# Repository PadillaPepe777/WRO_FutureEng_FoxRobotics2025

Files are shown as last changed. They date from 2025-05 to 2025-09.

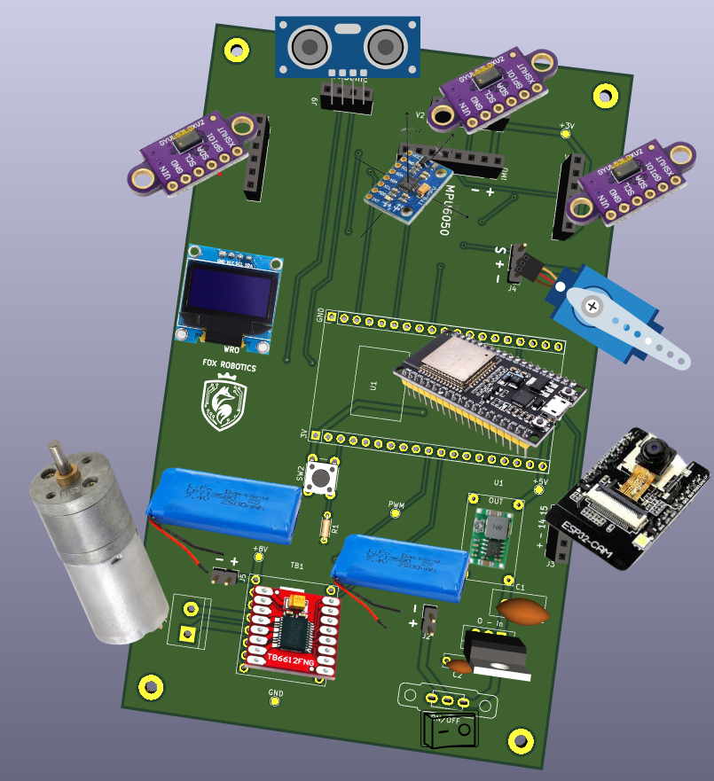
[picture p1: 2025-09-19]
Schemes/CircuitPlusComponents.png

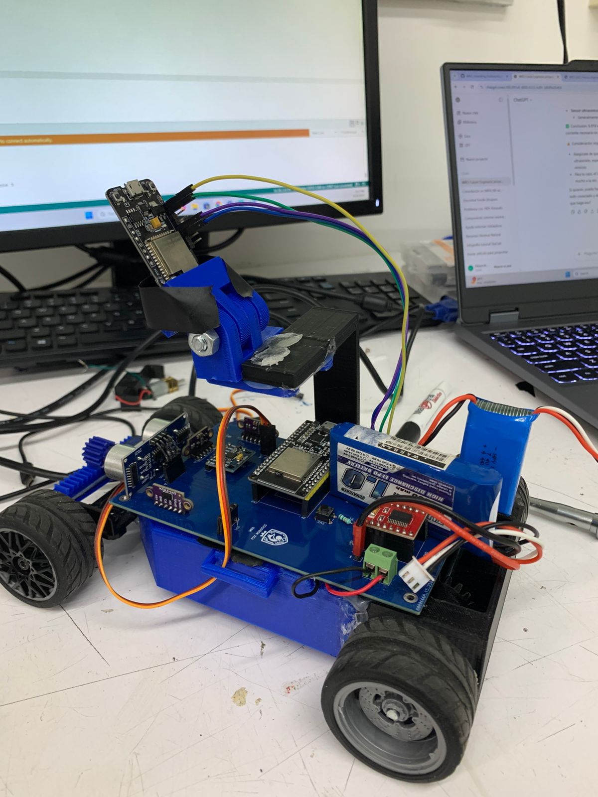
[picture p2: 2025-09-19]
v-photos/Img1.jpg

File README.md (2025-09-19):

The following repository is made with the intention of showing the work made by Luis Rodriguez and Alejandro Padilla for the FUTURE ENGINEERS WRO competition 2025.
The team decided to exploit all the capabilities of the ESP32 microcontroller family capabilities within the possibilities given by the ARDUINO IDE. The main functions of the Autonomous Car are made by the ESP32 WROOM Dev Module, which reads sensors and controls both steering and speed, while the ESP32-CAM its only in charge of color recognition, communicating the data with the ESP32 via Serial Communication. The Way the camera tracks colors is by making the image into kind of a matrix, identifying HSV values, dividing the image in 5-7 sections and communicating what color is the most present and where it’s located.

As it is our first prototype, we did the whole project on a perf board, but there are plans to make it into a professional PCB soon when we gather more resources. The wiring was designed on Ki-CAD, while the mechanical part was made in SolidWorks, a CAD software that our university gives us being students.
The car moves thanks to a Pololu motor in the back part, which pushes both wheels at the same speed thanks to a small gearbox, and the steering is in charge of your typical Servo motor of 90 grams.
The sensors used for the distance measurement were the VL53L0X ToF Infrarred sensors, which work with I2C communication. They have proven to be reliable once adjusted, and even though black objects can cause some trouble, we have worked as a team to find solutions. Apart from them, we are also using an MPU-6050 for accurate turns.

Since we aren’t using a computer like Raspberry, our prototype can run drawing little current, but still, we are using two different batteries to feed the circuit, one is for all the sensing and the brains, while other is just for the motor to run without problems. Both of them are 7.4 volts 600 mAh Li-po batteries, but for one of them we have a 5V regulator to avoid overheating in the microcontrollers. 
One of the attempts to use the ESP32 CAM was using AI with Edge Impulse, but instead of relying on them, we opted to use basic color tracking, which can be seen in the uploaded code. It’s worth noting that we used a version that already has USB compatibility, but the common one with or without Shield should be able to run it the same way. The only downside of this method is that we can’t see the ESP32 CAM view, we can only read what we receive from the Serial Console.

In another version we might unlock the ADC_2 pins to be able to connect to the internet or ESP-NOW for debugging purposes. But as for now we are sticking with what already worked for use, and this code can be useful for anyone trying to use Servos and Motors at the same time, because it’s quite different from Arduino and a bit harder to get this done in a ESP32.

Worth Mentioning This program works for the ESP32 board version 3.1.3

Latest Version can be found at WRO_Tijuana_Sept Folder

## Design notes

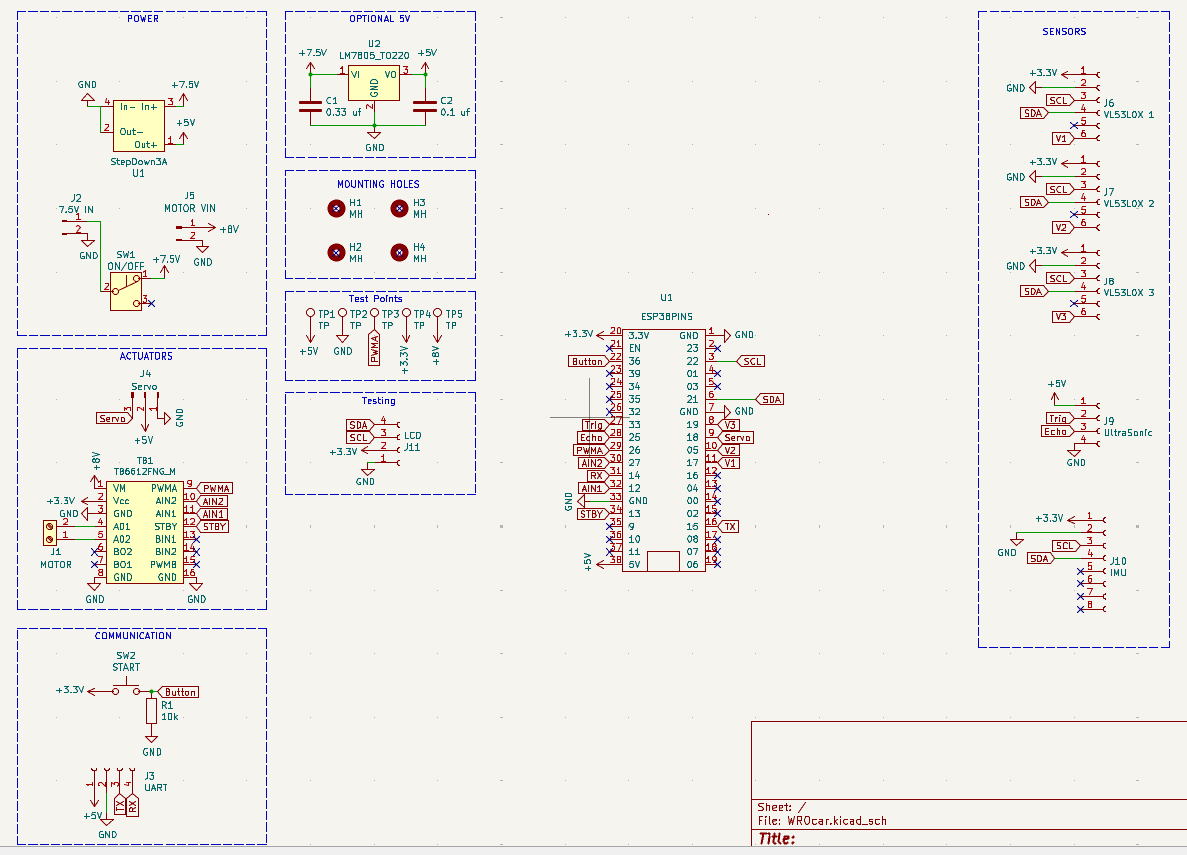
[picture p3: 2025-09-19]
Schemes/Schematic.png

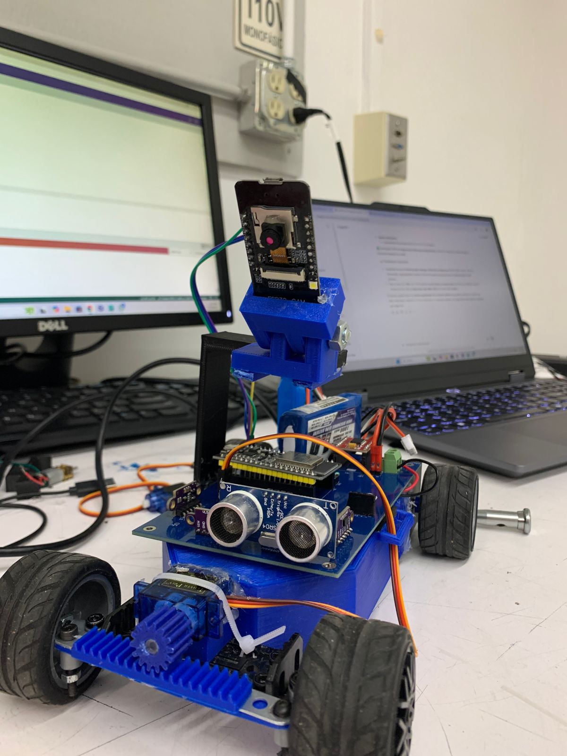
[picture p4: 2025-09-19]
v-photos/Im3.jpg

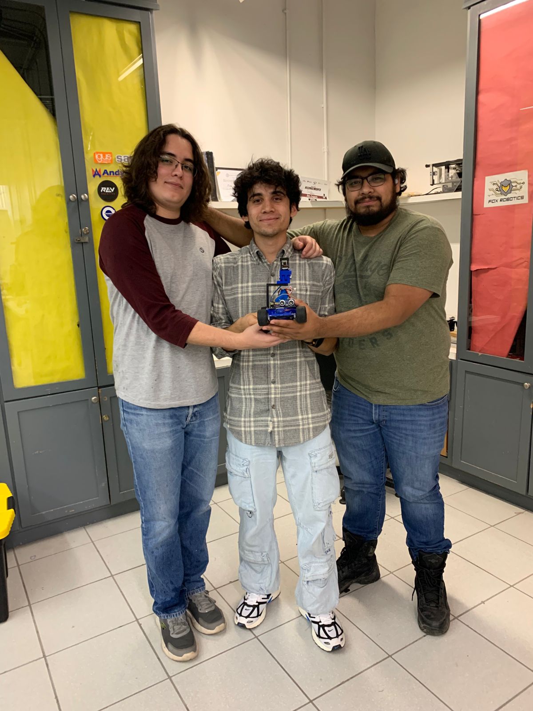
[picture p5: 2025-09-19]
t-photos/TeamPhoto.jpg

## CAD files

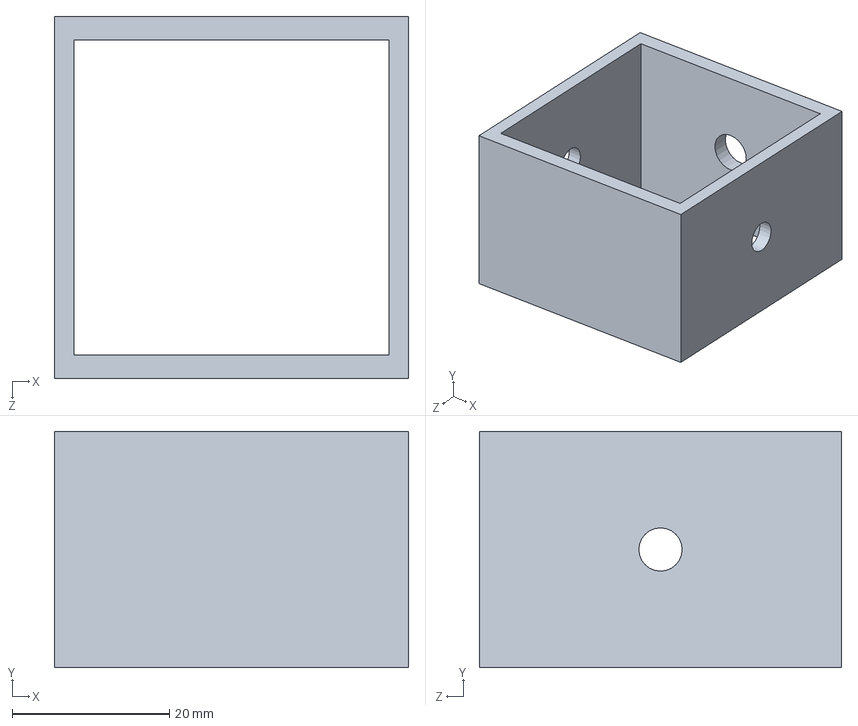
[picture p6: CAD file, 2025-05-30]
Schematic_MechanicalDesign/diferencial1.0.SLDPRT
45.0 x 30.0 x 46.0 mm

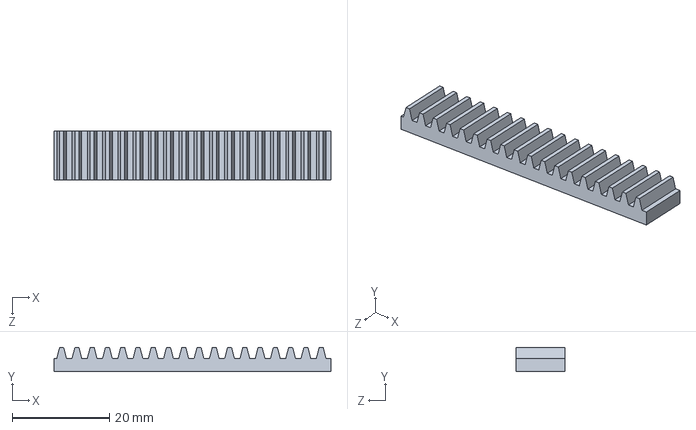
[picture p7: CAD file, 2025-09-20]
WRO_Tijuana_Sept/CAD-CAM/Metric - Rack-spur - rectangular 1M 14.5PA 10FW 4PH 57L---SAll.SLDPRT
57.0 x 5.00 x 10.0 mm

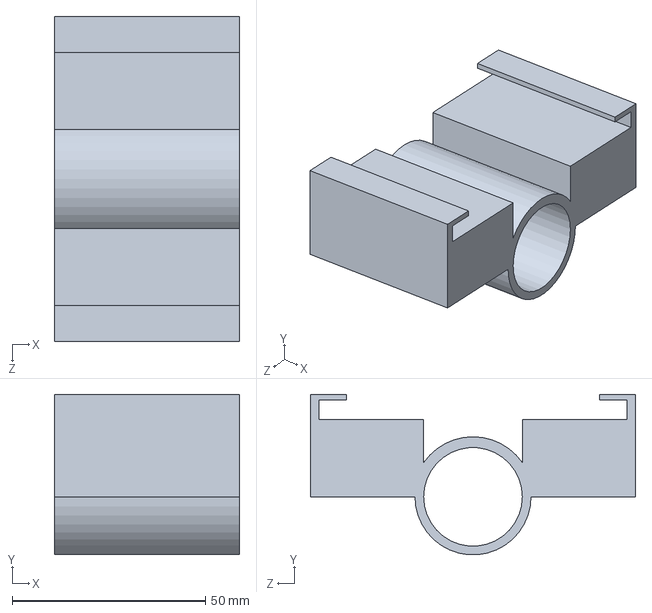
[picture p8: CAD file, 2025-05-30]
Schematic_MechanicalDesign/chasisquenoeschasis.SLDPRT
47.9 x 41.4 x 84.0 mm

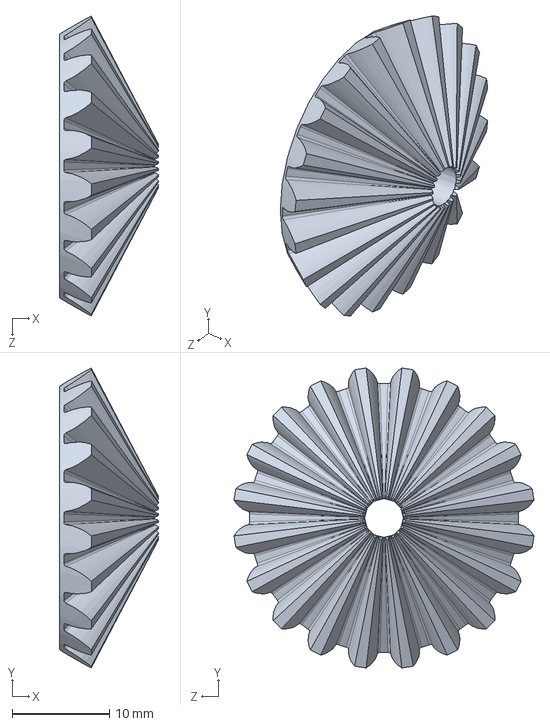
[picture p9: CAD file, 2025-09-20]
WRO_Tijuana_Sept/CAD-CAM/Metric - Straight bevel gear 1.5M 20GT 12PT 20PA 15FW ---20O10H11MD4N.SLDPRT
10.2 x 30.9 x 30.9 mm

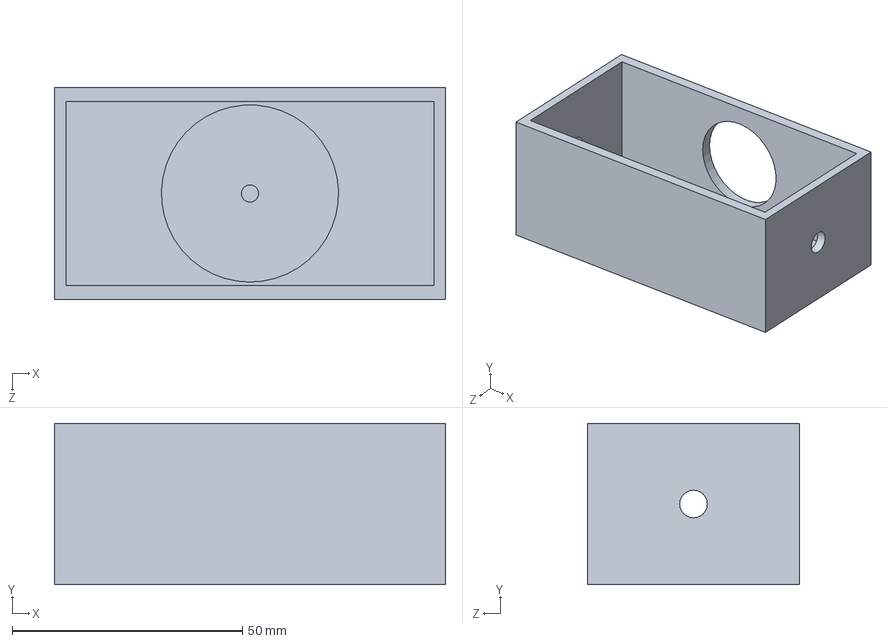
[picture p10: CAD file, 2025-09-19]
WRO_Tijuana_Sept/CAD-CAM/diferencial1.0.SLDPRT
85.0 x 35.0 x 46.0 mm

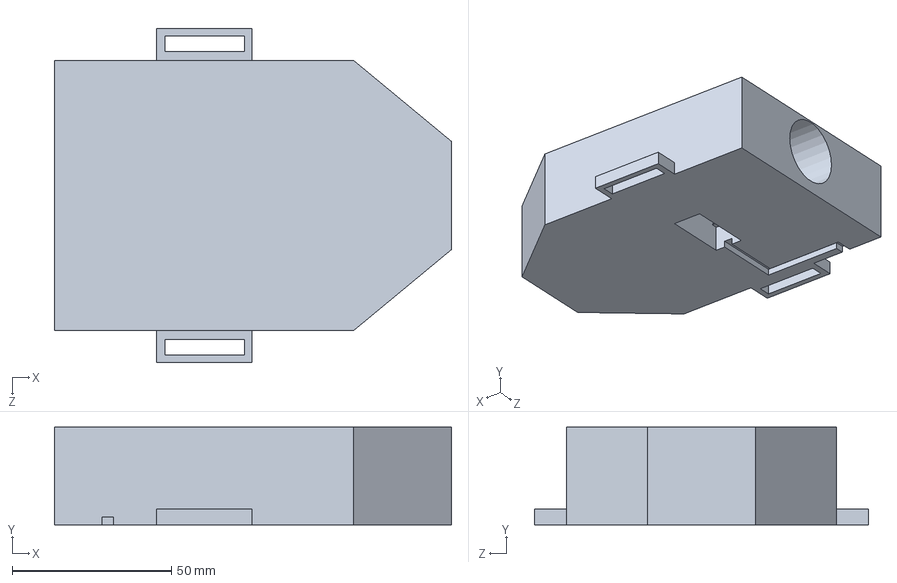
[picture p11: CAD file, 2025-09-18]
WRO_Tijuana_Sept/CAD-CAM/chasis.SLDPRT
124.8 x 30.8 x 105.0 mm

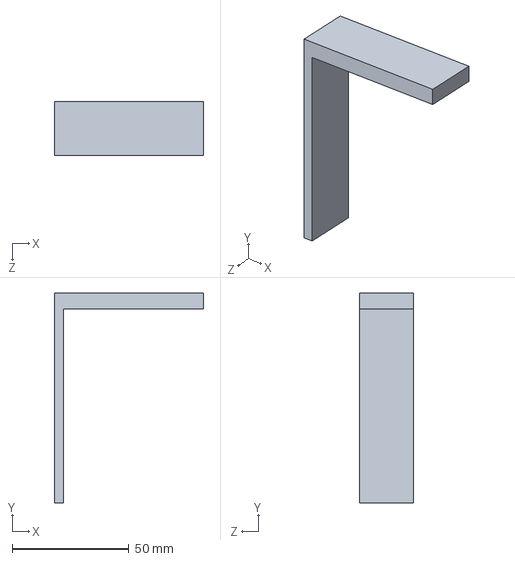
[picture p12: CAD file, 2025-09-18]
WRO_Tijuana_Sept/CAD-CAM/cam_s.SLDPRT
64.0 x 90.0 x 23.0 mm

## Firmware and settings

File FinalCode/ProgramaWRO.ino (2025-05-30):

#include <Arduino.h>

#include <Wire.h>
#include <VL53L0X.h>
#include <ESP32Servo.h>

VL53L0X sensor1; //derecha
VL53L0X sensor2; //delante
VL53L0X sensor3;//izquierda


#define XSHUT1  19  // Pin para apagar sensor 1
#define XSHUT2  5  // Pin para apagar sensor 2
#define XSHUT3  17 // Pin para apagar sensor 3

#define MOTOR_PWM_CHANNEL 2 // canal diferente al del servo
#define MOTOR_PWM_FREQ 12000
#define MOTOR_PWM_RESOLUTION 8

//Comunicacion Serial Colores
#define TX_PIN2 14  // Pin TX personalizado
#define RX_PIN2 15  // No se usa en el transmisor

int Numeros=0, Sector=0, Color=0;

String NOMBRE_COLORES[4] = {"Nada","Rojo", "Verde", "Magenta"};

float DERECHA, ENFRENTE, IZQUIERDA;

int dif,pos;
//Para Control PD
unsigned long currentTime, previousTime;
float elapsedTime;
double error, lastError, cumError, rateError;
//Distancia deseada
float Setpoint=0;
//Variables a Cambiar
float kp=3.8, kd=0.0001 ;

//IMU
int16_t Gyr_rawZ; //Read first Raw Data
float EgZ; //Data different from 0, avoids nan
float GradoRaw;
float AnguloZ=0.0;

unsigned long time1, timePrev, despliegue; //millis for integrals
//despliegue for showing angle every given time
float elapsedTime2;
float rad_to_deg = 180/3.141592654;
unsigned long Tvuelta;

float desired_angle = 0;

//Servo
int servoPin = 18;
Servo servo;

bool listo=false, listo2=false;
int casos=0;
float inicial=0.0;
int Esq=1, Vuelta=0;


//Motor
const int STBY=13;
const int PWM=27;
const int IN1=12;
const int IN2=26;
int Vel=170;

//Auxiliares
int i;
int ColorAnt, SectorAnt;
float auxColor, auxSector;
bool ModoColor=false;
float DLim=50, mult=0.75;

//Para serial
String linea;
String mensaje;


void setup() {


    Serial.begin(115200);
    delay(100);
    Serial2.begin(115200, SERIAL_8N1, RX_PIN2, TX_PIN2);
    Wire.begin(); //  SDA y SCL 40kHz
    delay(100);

    // Configurar pines XSHUT como salida
    pinMode(XSHUT1, OUTPUT);
    pinMode(XSHUT2, OUTPUT);
    pinMode(XSHUT3, OUTPUT);

    // Apagar ambos sensores
    digitalWrite(XSHUT1, LOW);
    digitalWrite(XSHUT2, LOW);
    digitalWrite(XSHUT3, LOW);
    delay(10);

    // Encender y configurar el primer sensor
    digitalWrite(XSHUT1, HIGH);
    delay(10);
    sensor1.setAddress(0x30);  // Cambiar dirección del sensor 1
    if (!sensor1.init()) {
        Serial.println("Error al iniciar Sensor 1");
    } else {
        Serial.println("Sensor 1 iniciado correctamente");
    }

    // Encender y configurar el segundo sensor
    digitalWrite(XSHUT2, HIGH);
    delay(10);
    sensor2.setAddress(0x31);  // Cambiar dirección del sensor 2
    if (!sensor2.init()) {
        Serial.println("Error al iniciar Sensor 2");
    } else {
        Serial.println("Sensor 2 iniciado correctamente");
    }

    digitalWrite(XSHUT3, HIGH);
    delay(10);
    sensor3.setAddress(0x32);  // Cambiar dirección del sensor 2
    if (!sensor3.init()) {
        Serial.println("Error al iniciar Sensor 3");
    } else {
        Serial.println("Sensor 3 iniciado correctamente");
    }

    // Iniciar medición en ambos sensores
    sensor1.startContinuous();
    sensor2.startContinuous();
    sensor3.startContinuous();

delay(100);

EgZ=0.0;

 Wire.beginTransmission(0x68);
    if (Wire.endTransmission() == 0) {  
        Wire.beginTransmission(0x68);
        Wire.write(0x6B);
        Wire.write(0);  // Sacar de modo sleep
        Wire.endTransmission(true);
        Serial.println("MPU6050 iniciado correctamente");
    } else {
        Serial.println("Error: MPU6050 no detectado.");
    }

    for(i=0;i<600;i++)
    {
    anguloIMU();
    EgZ+=Gyr_rawZ;
    delay(1);
    }
    
    EgZ=EgZ/600.0;

    Serial.print("Offsets: ");
    Serial.println(EgZ);

    delay(100);

    timePrev=millis();
    anguloIMUYa();
    Serial.print("Valores al momento: ");
   
        Serial.println(Gyr_rawZ);
        delay(100);

  servo.setPeriodHertz(50);             // 50 Hz para servo
  servo.attach(servoPin, 500, 2400);    // valores típicos: 500us (0°), 2400us (180°)
  Serial.println("Servo listo");

    pinMode(IN1,OUTPUT);
    pinMode(IN2,OUTPUT);
    pinMode(STBY,OUTPUT);
    digitalWrite(IN1, HIGH);
    digitalWrite(IN2, LOW);
    digitalWrite(STBY, HIGH);

ledcAttachChannel(PWM, MOTOR_PWM_FREQ, MOTOR_PWM_RESOLUTION, MOTOR_PWM_CHANNEL);

ledcAttachChannel(18, 50, 10, 1);

  servo.setPeriodHertz(50);
  servo.attach(18, 500, 2400);

 // ledcWrite(PWM, 200);  // valor entre 0-255 para 8 bits

linea ="";
while (linea.length() == 0) {
  if (Serial2.available()) {
    linea = Serial2.readStringUntil('\n');
    linea.trim(); // Limpia espacios y saltos de línea
    Serial.println("Recibido: " + linea);
  }
  delay(50);

}
}


void loop() {

//Habran switch cases para sentido horario, antihorario y colores con ambas variantes
//Para Hacer lo del angulo cuando se cumpla la condicion de pared enfrente, libre al lateral
//Seguir hasta haber una diferencia de 80 grados min entre inicial y actual

//Primero se va a detectar con comunicacion serial si hay colores o no, en caso de que no se ignora y se pasa al siguiente 

if (!listo){

    for(i=0;i<10;i++)
    {
        ReceiveSerial();
        Sector=Numeros%10;
        auxSector+=Sector;
      
          if(Sector==0)
        {
            Serial.println("No hay Color");
        }
          else
        {
            Color=(Numeros/10);
            auxColor+=1; //Para sacar promedio de cuantas veces se detecto color
            //Serial.println("Color: "+NOMBRE_COLORES[Color]+" En Sector "+String(Sector));
        }
    }

    //Aqui Sacamos un promedio de 10 lecturas, solo para comprobar antes de moverse si ve colores, si es asi...
    //podemos activar ModoColo como true, caso contrario leeremos mas adelante para comprobar y desactivar 
    //el modo mas adelante para evitar falsos positivos y consumir recursos

    auxColor=auxColor/10;

    //Mayor a %50 lo damos por bueno
    if(auxColor>0.5){
    ModoColor=true;
    Vel=150;
    }


  setLongRangeMode();
  ENFRENTE=(sensor2.readRangeContinuousMillimeters()/10.0);
  for(i=0; i<=50; i++)
  {
    ENFRENTE=(sensor2.readRangeContinuousMillimeters()/10.0);
    if(ENFRENTE<=300) break;
  }

  if(ENFRENTE>300.0)
  {
    setNormalMode();
    for(i=0; i<=50; i++)
  {
    ENFRENTE=(sensor2.readRangeContinuousMillimeters()/10.0);
    if(ENFRENTE<=300.0) break;
  }
  }

  if(ENFRENTE<=300.0)
  {
    inicial=ENFRENTE;
  }
  else
  {
    inicial=100.0;
  }
  listo=true;
}

setNormalMode();

ledcWrite(PWM, Vel);  // valor entre 0-255 para 8 bits

while(!listo2){

    Distancias();
    ColorAnt=0;

    if(DERECHA>=18 && IZQUIERDA>=18) //Cuidar que no estemos muy pegados 
    {
    ReceiveSerialFull();
    ColorAnt=Color;
    if(Sector>0)
    {
      ReceiveSerialFull();
      if(Sector>0 && ColorAnt==Color)
      {
        ModoColor=true;
        Vel=155;
        ledcWrite(PWM, Vel);  // valor entre 0-255 para 8 bits
        ActoColor();
      }
      else
      {
        Serial.println("Falsa Alarma");
      }
    }
    previousTime=millis();
    }
    else if(ENFRENTE<=DLim && IZQUIERDA>=90)
    {
    pos=10+(ENFRENTE*mult);
    casos=1;
    SetServo();

      delay(1);

      Tvuelta=timePrev=millis();
      while(abs(AnguloZ)<75.0)
      {
        anguloIMUYa();
        Serial.println(AnguloZ);
        if(millis()-Tvuelta>3000)
        break;
      }

      Serial.println("Ya salio");
      AnguloZ=0.0;
      
      pos=90;
      SetServo();
      delay(1);
      Distancias();

      while(IZQUIERDA>=90.0)
      {
        Distancias();
        dif= (DERECHA-35);  //para mantener pegado a un lado en lo que hay otro de referencia
        pos=PD_Centro (dif);
        ReceiveSerialFull();
        if(Sector>0 && (Color>0 && Color<4))
        {
          ReceiveSerialFull();
          if(Sector>0 && (Color>0 && Color<4))
          break;
        }
        Serial.println("Derecho");
      }
        
      previousTime=millis();
      break;
    }
      else if(ENFRENTE<=DLim && DERECHA>=90)
    {
    pos=170-(ENFRENTE*mult);
    casos=2;
    SetServo();
    delay(1);

      Tvuelta=timePrev=millis();
      
      while(abs(AnguloZ)<75.0)
      {
        anguloIMUYa();
        Serial.println(AnguloZ);
        if(millis()-Tvuelta>3000)
        break;
      }
      Serial.println("Ya salio");
      AnguloZ=0.0;

      pos=90;
      SetServo();
      while(DERECHA>=100.0)
      {
        Distancias();
        dif= (35-IZQUIERDA);  //para mantener pegado a un lado en lo que hay otro de referencia
        pos=PD_Centro (dif);

        ReceiveSerialFull(); //Volvemos a checar para evitar falsos positivos
        if(Sector>0 && (Color>0 && Color<4))
        {
          ReceiveSerialFull();
          if(Sector>0 && (Color>0 && Color<4))
          break;
        }
        Serial.println("Derecho");
      }
  
      previousTime=millis();
      break;
    }
    else if(DERECHA<100.0 && IZQUIERDA<100.0)
    {
    dif= (DERECHA-IZQUIERDA);
    pos=PD_Centro (dif);
    if(abs(pos)>4)
    {
    pos=90+pos;
    }
    else
    {
        pos=90;
    }
    }
    else
    pos=90;
    

    SetServo();
    delay(5);
}

listo2=true;

if(casos==1 && ModoColor==true)
casos=3;

if(casos==2 && ModoColor==true)
casos=4;
//Si se acaba la memoria, tal vez hacer los casos e irlos llamando porn turnos en el primer while, luego quedarse en uno solo

    switch(casos) {
      case 1:
      Serial.println("Sentido Antihorario No Color");
      while(Vuelta<3){

          if(Esq==4){
          Vuelta++;
          Esq=0;
          }
          if(Vuelta>=3)
          break;

        Distancias();

        if(ENFRENTE<=DLim && IZQUIERDA>=90)
    {
    pos=10+(ENFRENTE*mult);
    Esq++;
    SetServo();
      delay(1);

      Tvuelta=timePrev=millis();
      
      while(abs(AnguloZ)<75.0)
      {
        anguloIMUYa();
        Serial.println(AnguloZ);
        if(millis()-Tvuelta>3000)
        break;
      }
      Serial.println("Ya salio");
      AnguloZ=0.0;
    
      pos=90;
      SetServo();

      while(IZQUIERDA>=100.0){
        Distancias();
        dif= (DERECHA-35);  //para mantener pegado a un lado en lo que hay otro de referencia
        pos=PD_Centro (dif);
        Serial.println("Derecho");
      }

      previousTime=millis();
      //break;
    }
    else if(DERECHA<100.0 && IZQUIERDA<100.0)
    {
    dif= (DERECHA-IZQUIERDA);
    pos=PD_Centro (dif);

    if(abs(pos)>4)
    pos=90+pos;
    else
    pos=90;
    }
    else
    pos=90;

    SetServo();
    delay(5);

        if(Esq==4){
          Vuelta++;
          Esq=0;
        }
      }

      break;

      case 2:
      Serial.println("Sentido Horario No Color");
            while(Vuelta<3){

          if(Esq==4){
          Vuelta++;
          Esq=0;
          }
          if(Vuelta>=3)
          break;
            
        Distancias();

        if(ENFRENTE<=DLim && DERECHA>=90)
    {
    pos=170-(ENFRENTE*mult);
    Esq++;
    SetServo();
      delay(1);

      Tvuelta=timePrev=millis();
      
      while(abs(AnguloZ)<75.0)
      {
        anguloIMUYa();
        Serial.println(AnguloZ);
        if(millis()-Tvuelta>3000)
        break;
      }
      Serial.println("Ya salio");
      AnguloZ=0.0;
    
      pos=90;
      SetServo();

      while(DERECHA>=100.0){
        Distancias();
        dif= (35-IZQUIERDA);  //para mantener pegado a un lado en lo que hay otro de referencia
        pos=PD_Centro (dif);
        Serial.println("Derecho");
      }

      previousTime=millis();
      //break;
    }
    else if(DERECHA<100.0 && IZQUIERDA<100.0)
    {
    dif= (DERECHA-IZQUIERDA);
    pos=PD_Centro (dif);

    if(abs(pos)>4)
    pos=90+pos;
    else
    pos=90;
    }
    else
    pos=90;

    SetServo();
    delay(5);

        if(Esq==4){
          Vuelta++;
          Esq=0;
        }
      }

      break;

      case 3:

      Serial.println("Sentido Antihorario Color");

      //Estara Complicado
      while(Vuelta<3){

          if(Esq==4){
          Vuelta++;
          Esq=0;
          }
          if(Vuelta>=3)
          break;

          Distancias();
    ColorAnt=0;

    if(DERECHA>=18 && IZQUIERDA>=18) //Cuidar que no estemos muy pegados 
    {
    ReceiveSerialFull();
    ColorAnt=Color;
    if(Sector>0)
    {
      ReceiveSerialFull();
      if(Sector>0 && ColorAnt==Color)
      {
        ModoColor=true;
        Vel=155;
        ledcWrite(PWM, Vel);  // valor entre 0-255 para 8 bits
        ActoColor();
      }
      else
      {
        Serial.println("Falsa Alarma");
      }
    }
    previousTime=millis();
    }
    else if(ENFRENTE<=DLim && IZQUIERDA>=90)
    {
    pos=10+(ENFRENTE*mult);
    Esq++;

    SetServo();

      delay(1);

      Tvuelta=timePrev=millis();
      while(abs(AnguloZ)<75.0)
      {
        anguloIMUYa();
        Serial.println(AnguloZ);
        if(millis()-Tvuelta>3000)
        break;
      }

      Serial.println("Ya salio");
      AnguloZ=0.0;
      
      pos=90;
      SetServo();
      delay(1);
      Distancias();

      while(IZQUIERDA>=90.0)
      {
        Distancias();
        dif= (DERECHA-35);  //para mantener pegado a un lado en lo que hay otro de referencia
        pos=PD_Centro (dif);
        ReceiveSerialFull();
        if(Sector>0 && (Color>0 && Color<4))
        {
          ReceiveSerialFull();
          if(Sector>0 && (Color>0 && Color<4))
          break;
        }
        Serial.println("Derecho");
      }
        
      previousTime=millis();
      //break;
    }
    else if(DERECHA<100.0 && IZQUIERDA<100.0)
    {
    dif= (DERECHA-IZQUIERDA);
    pos=PD_Centro (dif);
    if(abs(pos)>4)
    {
    pos=90+pos;
    }
    else
    {
        pos=90;
    }
    }
    else
    pos=90;
    

    SetServo();
    delay(5);
            if(Esq==4){
          Vuelta++;
          Esq=0;
        }
      }

      break;

      case 4:

      Serial.println("Sentido Horario Color");
      //Definitivamente Complicado

      while(Vuelta<3){

          if(Esq==4){
          Vuelta++;
          Esq=0;
          }
          if(Vuelta>=3)
          break;

      Distancias();
    ColorAnt=0;

    if(DERECHA>=18 && IZQUIERDA>=18) //Cuidar que no estemos muy pegados 
    {
    ReceiveSerialFull();
    ColorAnt=Color;
    if(Sector>0)
    {
      ReceiveSerialFull();
      if(Sector>0 && ColorAnt==Color)
      {
        ModoColor=true;
        Vel=155;
        ledcWrite(PWM, Vel);  // valor entre 0-255 para 8 bits
        ActoColor();
      }
      else
      {
        Serial.println("Falsa Alarma");
      }
    }
    previousTime=millis();
    }
    else if(ENFRENTE<=DLim && IZQUIERDA>=90)
    {
    pos=10+(ENFRENTE*mult);
    casos=1;
    SetServo();

      delay(1);

      Tvuelta=timePrev=millis();
      while(abs(AnguloZ)<75.0)
      {
        anguloIMUYa();
        Serial.println(AnguloZ);
        if(millis()-Tvuelta>3000)
        break;
      }

      Serial.println("Ya salio");
      AnguloZ=0.0;
      
      pos=90;
      SetServo();
      delay(1);
      Distancias();

      while(IZQUIERDA>=90.0)
      {
        Distancias();
        dif= (DERECHA-35);  //para mantener pegado a un lado en lo que hay otro de referencia
        pos=PD_Centro (dif);
        ReceiveSerialFull();
        if(Sector>0 && (Color>0 && Color<4))
        {
          ReceiveSerialFull();
          if(Sector>0 && (Color>0 && Color<4))
          break;
        }
        Serial.println("Derecho");
      }
        
      previousTime=millis();
      break;
    }
      else if(ENFRENTE<=DLim && DERECHA>=90)
    {
    pos=170-(ENFRENTE*mult);
    casos=2;
    SetServo();
    delay(1);

      Tvuelta=timePrev=millis();
      
      while(abs(AnguloZ)<75.0)
      {
        anguloIMUYa();
        Serial.println(AnguloZ);
        if(millis()-Tvuelta>3000)
        break;
      }
      Serial.println("Ya salio");
      AnguloZ=0.0;

      pos=90;
      SetServo();
      while(DERECHA>=100.0)
      {
        Distancias();
        dif= (35-IZQUIERDA);  //para mantener pegado a un lado en lo que hay otro de referencia
        pos=PD_Centro (dif);

        ReceiveSerialFull(); //Volvemos a checar para evitar falsos positivos
        if(Sector>0 && (Color>0 && Color<4))
        {
          ReceiveSerialFull();
          if(Sector>0 && (Color>0 && Color<4))
          break;
        }
        Serial.println("Derecho");
      }
  
      previousTime=millis();
      //break;
    }
    else if(DERECHA<100.0 && IZQUIERDA<100.0)
    {
    dif= (DERECHA-IZQUIERDA);
    pos=PD_Centro (dif);
    if(abs(pos)>4)
    {
    pos=90+pos;
    }
    else
    {
        pos=90;
    }
    }
    else
    pos=90;
    
    SetServo();
    delay(5);

          if(Esq==4){
          Vuelta++;
          Esq=0;
        }

}

      break;

      default:

      Serial.println("Espero esto no suceda");

      break;
    }

    if(casos <=2)
    {
    Distancias();
    servo.write(90);
    Tvuelta=millis();
    while(ENFRENTE<inicial)
    {
      Distancias();
      if(millis()-Tvuelta>=2000)
      break;
    }
    }

    if(casos==3) //Antihorario color
    { 
    Vel=140;
    ledcWrite(PWM, Vel);  // valor entre 0-255 para 8 bits
    Tvuelta=millis();

    while(Color!=4 && Sector<=3)
    {
      Distancias();
      if(DERECHA<=90)
      dif=(DERECHA-IZQUIERDA);
      else
      dif=(35-IZQUIERDA);

      pos=PD_Centro (dif);
      SetServo();

      ReceiveSerialFull();

      if(millis()-Tvuelta>=10000)
      break;;
    }
    pos=150;
    SetServo();
    
    Tvuelta=millis();
    while(ENFRENTE>12.0)
    {
      Distancias();
      if(millis()-Tvuelta>=2000)
      break;
    }
    }

    if(casos==4) //Antihorario color
    { 
    Vel=140;
    ledcWrite(PWM, Vel);  // valor entre 0-255 para 8 bits
    Tvuelta=millis();


    while(Color!=4 && Sector>=3)
    {
      Distancias();
      if(IZQUIERDA<=90)
      dif=(DERECHA-IZQUIERDA);
      else
      dif=(DERECHA-35);
    
      pos=PD_Centro (dif);
      SetServo();

      ReceiveSerialFull();

      if(millis()-Tvuelta>=10000)
      break;
    }
    pos=30;
    SetServo();
    Tvuelta=millis();
    while(ENFRENTE>12.0)
    {
      Distancias();
      if(millis()-Tvuelta>=2000)
      break;
    }
    }

    //FIN DEL PROGRAMA

    Vel=0;
    ledcWrite(PWM, Vel);  // valor entre 0-255 para 8 bits

    while(1)
    {
      Serial.println("Esto es todo amigos");
      delay(500);
    }

    //Si llegan a haber problemas para parkearse, poner otra condicion para buscar magenta en la vuelta 2 Esq 4

}

int PD_Centro (int input) {
 
    currentTime = millis();                          // obtener el tiempo actual
    elapsedTime = (currentTime - previousTime)/1000.0;     // calcular el tiempo transcurrido
        
    error = input;                               // determinar el error entre la consigna y la medición
    rateError = (error - lastError) / elapsedTime;       // calcular la derivada del error
 
    int output = kp*error + kd*rateError;     // calcular la salida del PID

    if(output>50)
    {
      output=50;
    }
    if(output<-50)
    {
      output=-50;
    }

    lastError = error;                                    // almacenar error anterior
    previousTime = currentTime;                           // almacenar el tiempo anterior
 
    return output;
}

void anguloIMUYa () {
   // the previous time is stored before the actual time read
    time1 = millis();  // actual time read
    elapsedTime2 = (time1 - timePrev) / 1000.0; 
    
   Wire.beginTransmission(0x68);
   Wire.write(0x47); //Gyro data first adress
   Wire.endTransmission(false);
   Wire.requestFrom(0x68,2,true); //Just  registers
   
   Gyr_rawZ=Wire.read()<<8|Wire.read();

   GradoRaw=(Gyr_rawZ-EgZ)/131.0;

   if(abs(GradoRaw*elapsedTime2)>=0.06)
   AnguloZ+= GradoRaw*elapsedTime2;

  timePrev = time1;
}


void anguloIMU () {
   // the previous time is stored before the actual time read
    time1 = millis();  // actual time read
    elapsedTime2 = (time1 - timePrev) / 1000.0; 
    
   Wire.beginTransmission(0x68);
   Wire.write(0x47); //Gyro data first adress
   Wire.endTransmission(false);
   Wire.requestFrom(0x68,2,true); //Just  registers
   
   Gyr_rawZ=Wire.read()<<8|Wire.read();

  timePrev = time1;
}

void setLongRangeMode() {
  sensor2.stopContinuous();
  sensor2.setSignalRateLimit(0.1); // menor = más alcance
  sensor2.setVcselPulsePeriod(VL53L0X::VcselPeriodPreRange, 18);
  sensor2.setVcselPulsePeriod(VL53L0X::VcselPeriodFinalRange, 14);
  sensor2.startContinuous();
  Serial.println("Modo: Largo alcance activado");
}

void setNormalMode() {
  sensor2.stopContinuous();
  sensor2.setSignalRateLimit(0.25); // valor por defecto
  sensor2.setVcselPulsePeriod(VL53L0X::VcselPeriodPreRange, 14);
  sensor2.setVcselPulsePeriod(VL53L0X::VcselPeriodFinalRange, 10);
  sensor2.startContinuous();
  Serial.println("Modo: Normal restaurado");
}

void Distancias(){
    DERECHA=(sensor1.readRangeContinuousMillimeters()/10.0)-1.2;
    delay(1);
    ENFRENTE=(sensor2.readRangeContinuousMillimeters()/10.0)-6.5;
    delay(1);
    IZQUIERDA=(sensor3.readRangeContinuousMillimeters()/10.0)-4.3;
    delay(1);

    Serial.print("Distancia Sensor 1: ");
    Serial.print(DERECHA);

    Serial.print("   Distancia Sensor 2: ");
    Serial.print(ENFRENTE);

    Serial.print("   Distancia Sensor 3: ");
    Serial.println(IZQUIERDA);
}

void ReceiveSerial(){

    unsigned long timeout=millis();
    mensaje="";
    while(mensaje.length() == 0) {
    Serial.println("Esperando...");
    if(millis()-timeout>=500)
    break;
    delay(1);
    if (Serial2.available()) {
        mensaje = Serial2.readStringUntil('\n');
        mensaje.trim();
        Numeros = mensaje.toInt();
    }
}
}

void SetServo(){
    if(pos>135)
    pos=135;

    if(pos<45)
    pos=45;

    servo.write(pos);
    Serial.print("Servo a: ");
    Serial.println (pos);
    delay(5);
}
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

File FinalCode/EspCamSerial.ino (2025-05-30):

// ESP32-CAM con detección de color usando HSV y 5 cuadrantes
#include "esp_camera.h"
#include "Arduino.h"
#include "driver/uart.h"

// Configuración de pines
#define PWDN_GPIO_NUM     32
#define RESET_GPIO_NUM    -1
#define XCLK_GPIO_NUM      0
#define SIOD_GPIO_NUM     26
#define SIOC_GPIO_NUM     27
#define Y9_GPIO_NUM       35
#define Y8_GPIO_NUM       34
#define Y7_GPIO_NUM       39
#define Y6_GPIO_NUM       36
#define Y5_GPIO_NUM       21
#define Y4_GPIO_NUM       19
#define Y3_GPIO_NUM       18
#define Y2_GPIO_NUM        5
#define VSYNC_GPIO_NUM    25
#define HREF_GPIO_NUM     23
#define PCLK_GPIO_NUM     22

#define TX_PIN 14
#define RX_PIN 15

const int W = 160;
const int H = 120;

const int NUM_COLORES = 3;
const int HUE_MIN[NUM_COLORES] = {2, 60, 290};
const int HUE_MAX[NUM_COLORES] = {10, 90, 320};
const int SAT_MIN[NUM_COLORES] = {120, 120, 120};
const int SAT_MAX[NUM_COLORES] = {255, 255, 255};
const int VAL_MIN[NUM_COLORES] = {120, 120, 120};
const int VAL_MAX[NUM_COLORES] = {255, 255, 255};
//const char *NOMBRE_COLORES[NUM_COLORES] = {"Rojo", "Verde", "Magenta"};
const int NOMBRE_COLORES[NUM_COLORES]={10,20,30};

//String auxColor;
int auxColor;
int ubi = -1;
int colorDetectado = -1;
uint8_t *mask_buffer;

void setup() {
  Serial.begin(115200);
  Serial2.begin(115200, SERIAL_8N1, RX_PIN, TX_PIN);

  camera_config_t config;
  config.ledc_channel = LEDC_CHANNEL_0;
  config.ledc_timer = LEDC_TIMER_0;
  config.pin_d0 = Y2_GPIO_NUM;
  config.pin_d1 = Y3_GPIO_NUM;
  config.pin_d2 = Y4_GPIO_NUM;
  config.pin_d3 = Y5_GPIO_NUM;
  config.pin_d4 = Y6_GPIO_NUM;
  config.pin_d5 = Y7_GPIO_NUM;
  config.pin_d6 = Y8_GPIO_NUM;
  config.pin_d7 = Y9_GPIO_NUM;
  config.pin_xclk = XCLK_GPIO_NUM;
  config.pin_pclk = PCLK_GPIO_NUM;
  config.pin_vsync = VSYNC_GPIO_NUM;
  config.pin_href = HREF_GPIO_NUM;
  config.pin_sccb_sda = SIOD_GPIO_NUM;
  config.pin_sccb_scl = SIOC_GPIO_NUM;
  config.pin_pwdn = PWDN_GPIO_NUM;
  config.pin_reset = RESET_GPIO_NUM;
  config.xclk_freq_hz = 20000000;
  config.pixel_format = PIXFORMAT_RGB565;
  config.frame_size = FRAMESIZE_QQVGA;
  config.jpeg_quality = 12;
  config.fb_count = 1;

  if (esp_camera_init(&config) != ESP_OK) {
    Serial.println("Error al iniciar la camara");
    return;
  }

  mask_buffer = (uint8_t *)malloc(W * H);
  if (!mask_buffer) {
    Serial.println("Error: No hay suficiente RAM.");
  }
}


//Los cuadrantes van de Izq a Der, cada color es una decena, los cuadrantes unidades, con función de residuo obtendremos el valor
void loop() {
  if (!mask_buffer) {
    ESP.restart();
  }

  camera_fb_t *fb = esp_camera_fb_get();
  if (!fb) return;

  process_image(fb->buf, mask_buffer);
  show_result();

  esp_camera_fb_return(fb);

  Serial2.println(auxColor);
  Serial2.flush();

  delay(100);
}

void process_image(uint8_t *imageIn, uint8_t *mask_buffer) {
  long suma_x = 0;
  int cuenta = 0;
  colorDetectado = -1;

  for (int i = 0; i < W * H; i++) {
    uint8_t r = (imageIn[i * 2] & 0xF8);
    uint8_t g = ((imageIn[i * 2] & 0x07) << 5) | ((imageIn[i * 2 + 1] & 0xE0) >> 3);
    uint8_t b = (imageIn[i * 2 + 1] & 0x1F) << 3;

    uint8_t maxVal = max(r, max(g, b));
    uint8_t minVal = min(r, min(g, b));
    uint8_t delta = maxVal - minVal;

    float h = 0;
    if (delta > 0) {
      if (maxVal == r) h = 60 * ((g - b) / (float)delta);
      else if (maxVal == g) h = 60 * (2 + (b - r) / (float)delta);
      else h = 60 * (4 + (r - g) / (float)delta);
      if (h < 0) h += 360;
    }
    uint8_t s = (maxVal == 0) ? 0 : (delta * 255 / maxVal);
    uint8_t v = maxVal;

    for (int c = 0; c < NUM_COLORES; c++) {
      if (h >= HUE_MIN[c] && h <= HUE_MAX[c] &&
          s >= SAT_MIN[c] && s <= SAT_MAX[c] &&
          v >= VAL_MIN[c] && v <= VAL_MAX[c]) {
        int x = i % W;
        suma_x += x;
        cuenta++;
        colorDetectado = c;
        break;
      }
    }
  }

  if (cuenta > 0) {
    int x_prom = suma_x / cuenta;
    if (x_prom < 32) ubi = 1;
    else if (x_prom < 64) ubi = 2;
    else if (x_prom < 96) ubi = 3;
    else if (x_prom < 128) ubi = 4;
    else ubi = 5;
  } else {
    colorDetectado = -1;
    ubi = 0;
  }
}

void show_result() {
  if (colorDetectado == -1) {
    auxColor = 0;
    Serial.println("Nada detectado");
  } else {
    auxColor = (NOMBRE_COLORES[colorDetectado]+ubi);
    Serial.print("Color "); Serial.print(auxColor);
    Serial.print(" detectado en cuadrante "); Serial.println(ubi);
  }
}

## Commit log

2025-05-17 Add files via upload
    Este es el primer programa base para WRO, sirve mas para prueba de sensores y control PD de Servo para orientación del vehículo
2025-05-17 Add files via upload
    Programa Para la ESP32 Cam para detectar Colores en 7 sectores divididos horizontalmente, con comunicación Serial
2025-05-29 Add files via upload
    Made in KiCad
2025-05-29 Add files via upload
    Just need to figure out the Color Mode for case 3 and 4, should just be repeating code from the first part with minor modifications I guess
2025-05-30 Create Puede ser el final
2025-09-18 Add files via upload
    Testing Software with I2C Oled display
    Useful to debugging, calibrating sensors and testing both motors and direction
